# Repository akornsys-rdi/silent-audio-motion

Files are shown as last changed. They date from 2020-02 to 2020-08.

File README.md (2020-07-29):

# Silent audio motion

Silent audio motion, the system behind «Ver no es hablar» artwork

## Description

The device generates the movement of a magnet according to an input audio signal. For this purpose the device generates a PWM signal with polarity (positive and negative half cycle) to excite an electromagnet. This signal is proportional to an analog input signal (audio source). It has two symmetrical channels and it responds to different frequencies, signal levels and waveforms.

This repository includes all the necessary files of this project: The 3D files to be printed, the control board of the device and its firmware.

### Technical features

- Supply voltage: 12VDC
- Frequency range: 1KHz-0.1Hz (firmware capability)
- Input voltage: up to 3Vpp
- Input impedance: 20kΩ

### Status LED

The device includes an LED to show the state it is in, these states are:

- Permanent LED indicates that there is no signal on either channel, the output driver is off.
- Slow blinking LED (~8Hz) indicates clipping on output, input level needs to be lowered or ADJ trimmer needs to be adjusted if not calibrated.
- Fast flashing LED (~30Hz) indicates input level too high, input level needs to be lowered, input stage may be damaged.
- LED off in normal operation.

The status LED may take up to one second to respond to changes in the input.

## Testing the device

### Output driver test

Load the `test_outputs` program. It should generate signals on both output channels. The test firmware can generate different output patterns.
The test is successful when the solenoid connected to each channel moves at the frequency set in code, with the selected waveform.

### Input stage test

Load the 'test_inputs' program. The cursor of the trimmers must not be at the ends. This program must show per port the three inputs of each channel (use serial plotter). Connect an audio source with a signal below 10Hz to both channels.

The test is successful when:

- The values of the first and fourth signals should be the values of the inputs of the left and right audio channels respectively.
- The values of the second and fifth signals should be the values of the ADJ trimmers, and should be different from the ends.
- The values of the third and sixth signals are a comparison of the negative half-cycle with the TRG trimmers, and should show a square signal centered on the peaks of the audio inputs. If this square signal does not appear, move the TRG trimmers until it does.

One of the input signal half-cycles may be slightly smaller than the other.

## Calibrating the device

Set the 3Hz and 3Vpp sine wave signal to channel L, with the program 'test_inputs' loaded.

Adjust the ADJ trimmer immediately above the peak of the input signal, and below the STANDBY_THRESHOLD threshold (default 900). A good value is 817. Turning it counterclockwise increases the value, and turning it clockwise decreases it.

Change the frequency to 0.5Hz. Adjust the ADJ trimmer until it is as close to zero as possible. It should be shown only during negative half-cycles. Values too low show square signals during both half-cycles. Values too high are far from zero on negative half-cycles.
A good adjustment is to lower it until it is below zero and to go up until the trigger disappears in the positive semicircle, then add a quarter turn more. Turning clockwise lowers the value, turning counterclockwise raises it.

Repeat the process with the R channel.

Enter signal on both channels, the setting signals must overlap.

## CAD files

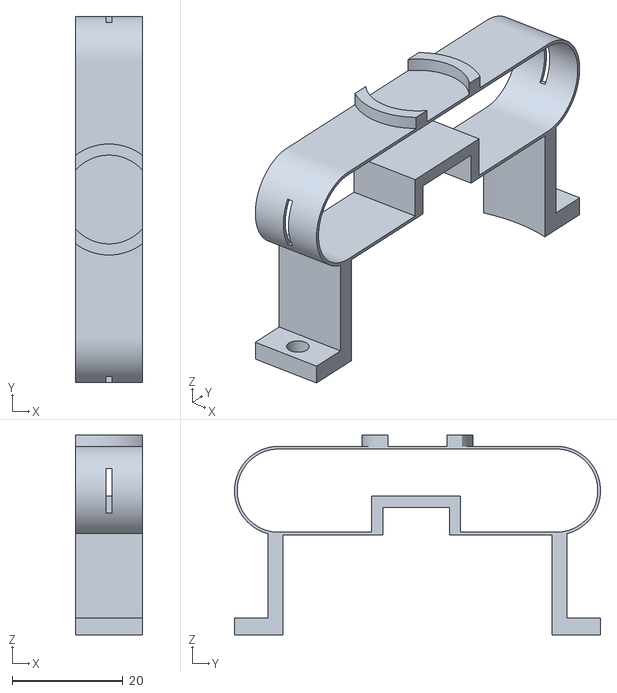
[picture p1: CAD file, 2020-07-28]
3d/bridge.stl
12.0 x 66.0 x 36.0

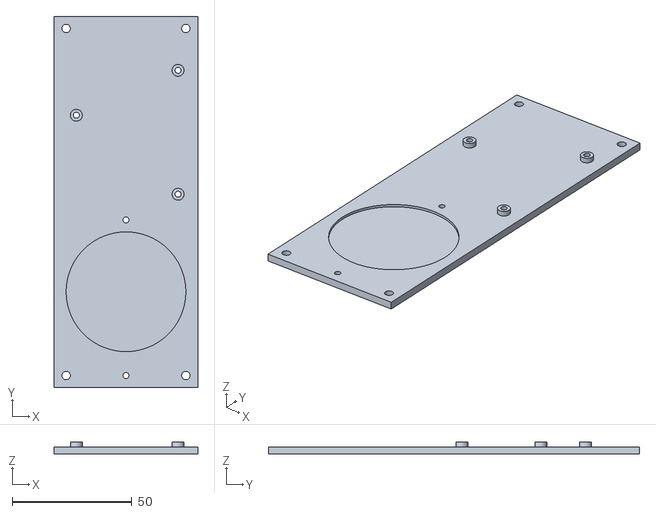
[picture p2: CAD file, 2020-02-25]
3d/base.stl
60.0 x 155.0 x 5.00

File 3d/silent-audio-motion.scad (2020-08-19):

$fn=36;

base();
translate([53,0,1]) cover();
translate([26,37,3]) bridge_v3();
translate([26,37,0]) solenoid();
translate([26,37,3.5+21+12.5]) magnet();
translate([105,72,3]) rotate([0,0,180]) pcb();

module base() {
    radius = 4;
    size_x = 107;
    size_y = 74;
    padding_x = 53;
    padding_y = 4;

    difference() {
        union() {
            union() {
                hull() {
                    for (i = [ [radius,radius + padding_y,0], [radius,size_y - radius - padding_y,0], [padding_x - radius,size_y - radius - padding_y,0], [padding_x - radius,radius + padding_y,0] ]) {
                        translate(i) cylinder(r=radius, h=1);
                    }
                }
                hull() {
                    for (i = [ [padding_x - radius*2,radius + padding_y,0], [padding_x - radius*2,size_y - radius - padding_y,0], [padding_x,radius,0], [padding_x,size_y - radius,0] ]) {
                        translate(i) cylinder(r=radius, h=1);
                    }
                }
                hull() {
                    for (i = [ [padding_x,radius,0], [padding_x,size_y - radius,0], [size_x - radius,size_y - radius,0], [size_x - radius,radius,0] ]) {
                        translate(i) cylinder(r=radius, h=1);
                    }
                }
                hull() {
                    for (i = [ [size_x - radius,radius,0], [size_x + radius,radius,0] ]) {
                        translate(i) cylinder(r=radius, h=1);
                    }
                }
                //refuerzos
                for (i = [ [5,7,1], [5,11,1], [5,67,1], [5,63,1] ]) {
                    hull() {
                        for (j = [0:1:1]) {
                            translate(i) translate([0,0,j]) sphere(r=1, $fn=36);
                            translate(i) translate([45,0,j]) sphere(r=1, $fn=36);
                        }
                    }
                }
            }
            //bridge
            translate([20,padding_y, 0]) cube([12,size_y - padding_y*2, 3]);
            //puntos montaje base
            translate([size_x + radius,radius,0]) cylinder(r=radius, h=3);
            translate([radius,size_y - radius - padding_y,0]) cylinder(r=radius, h=3);
            //punto montaje pcb
            translate([58.25,16.5,0]) cylinder(r=3.5, h=3.25);
            translate([58.25,68.25,0]) cylinder(r=3.5, h=3.25);
            translate([100.75,35.25,0]) cylinder(r=3.5, h=3.25);
        }
        union() {
            //solenoide
            translate([26,37,-1]) cylinder(r=24.5, h=5);
            //vaciado pcb
            hull() {
                for (i = [ [60,25,-1], [60,60,-1], [75,10,-1], [92,60,-1], [92,10,-1] ]) {
                    translate(i) cylinder(r=3, h=3);
                }
            }
            //taladros montaje bridge
            translate([26,7,-1]) cylinder(r=1.25, h=5);
            translate([26,67,-1]) cylinder(r=1.25, h=5);
            //taladros montaje pcb
            translate([58.25,16.5,-1]) cylinder(r=1.25, h=5);
            translate([58.25,68.25,-1]) cylinder(r=1.25, h=5);
            translate([100.75,35.25,-1]) cylinder(r=1.25, h=5);
            //taladros montaje base
            translate([size_x + radius,radius,-1]) cylinder(r=1.75, h=5);
            translate([size_x + radius,radius,0.1]) cylinder(r1=1.75, r2=3, h=3.1);
            translate([radius,size_y - radius - padding_y,-1]) cylinder(r=1.75, h=5);
            translate([radius,size_y - radius - padding_y,0.1]) cylinder(r1=1.75, r2=3, h=3.1);
        }
    }
}

module cover() {
    difference() {
        union() {
            hull() {
                for(i = [ [3,3,0], [3,71,0], [51,3,0], [51,71,0] ]) {
                    translate(i) cylinder(r=3, h=20);
                }
            }
            union() {
                translate([6.75+5.25,0.5,5]) rotate([90,0,0]) linear_extrude(1) text("L", font=":bold", size=4, valign="center", halign = "center");
                translate([6.75,0.5,14]) rotate([90,270,0]) linear_extrude(1) text("TRG", font=":bold", size=4, valign="center", halign = "center");
                translate([6.75+10.5,0.5,14]) rotate([90,270,0]) linear_extrude(1) text("ADJ", font=":bold", size=4, valign="center", halign = "center");
                translate([6.75+5.25+21,0.5,5]) rotate([90,0,0]) linear_extrude(1) text("R", font=":bold", size=4, valign="center", halign = "center");
                translate([6.75+21,0.5,14]) rotate([90,270,0]) linear_extrude(1) text("ADJ", font=":bold", size=4, valign="center", halign = "center");
                translate([6.75+31.5,0.5,14]) rotate([90,270,0]) linear_extrude(1) text("TRG", font=":bold", size=4, valign="center", halign = "center");
                translate([53.5,25,17]) rotate([90,0,90]) linear_extrude(1) text("IN", font=":bold", size=4, valign="center", halign = "center");
                translate([53.5,41.6+2.54,13]) rotate([90,0,90]) linear_extrude(1) text("L", font=":bold", size=4, valign="center", halign = "center");
                translate([53.5,41.6+10.16+2.54,13]) rotate([90,0,90]) linear_extrude(1) text("R", font=":bold", size=4, valign="center", halign = "center");
                translate([53.5,41.6+20.32,13]) rotate([90,0,90]) linear_extrude(1) text("-", font=":bold", size=6, valign="center", halign = "center");
                translate([53.5,41.6+20.32+5.08,13]) rotate([90,0,90]) linear_extrude(1) text("+", font=":bold", size=5, valign="center", halign = "center");
            }
        }
        union() {
            //ventilacion
            translate([10.25,10.25,18]) for(i = [0:7:30]) {
                for(j = [0:7:50]) {
                    translate([i,j,0]) cube([4.5,4.5,3]);
                }
            }
            //puntos de montaje
            difference() {
                hull() {
                    for(i = [ [4,4,-1], [4,70,-1], [50,4,-1], [50,70,-1] ]) {
                        translate(i) cylinder(r=3, h=20);
                    }
                }
                translate([5.25,16.5,3.75]) cylinder(r=3.75, h=17);
                translate([5.25,68.25,3.75]) cylinder(r=3.75, h=17);
                translate([47.75,35.25,3.75]) cylinder(r=3.75, h=17);
            }
            //pot
            translate([6.75,2,7.1]) for(i = [0:10.5:35]) {
                translate([i,0,0]) rotate([90,0,0]) cylinder(r=1.5, h=3);
            }
            //jack
            translate([52,25,10]) hull() {
                rotate([0,90,0]) cylinder(r=4, h=3);
                translate([0,0,-10]) rotate([0,90,0])  cylinder(r=4, h=3);
            }
            //conn
            translate([52,39.6,0]) for(i = [0:5.08:26]) {
                translate([0,i,6]) cube([3,4,4.5]);
                translate([-4,i+2,18]) cylinder(r=2.5, h=3);
            }
            //puntos de montaje
            union() {
                translate([5.25,16.5,3]) cylinder(r=1.75, h=3);
                translate([5.25,68.25,3]) cylinder(r=1.75, h=3);
                translate([47.75,35.25,3]) cylinder(r=1.75, h=3);
                translate([5.25,16.5,4.75]) cylinder(r=2.85, h=16);
                translate([5.25,68.25,4.75]) cylinder(r=2.85, h=16);
                translate([47.75,35.25,4.75]) cylinder(r=2.85, h=16);
            }
        }
    }
}

module bridge_v3() {
    thickness = 0.5;
    aperture = 1;
    lenght = 50;

    difference() {
        union() {
            //base
            translate([-6,-33,0]) cube([12,66,3]);
            translate([-6,-27,0]) cube([12,54,32.5]);
            //anillo
            translate([-6,-(lenght/2),26]) hull() {
                rotate([0,90,0]) cylinder(r=8, h=12);
                translate([0,lenght,0]) rotate([0,90,0]) cylinder(r=8, h=12);
            }
            //soporte iman
            translate([0,0,34]) cylinder(r=10, h=2);
        }
        union() {
            //solenoide
            translate([0,0,-1]) cylinder(r=25, h=19);
            //apertura
            translate([(12-aperture)/2-6,-(lenght/2)-10,22]) cube([aperture,10,8]);
            translate([(12-aperture)/2-6,(lenght/2),22]) cube([aperture,10,8]);
            //hueco anillo
            difference() {
                translate([-7,-(lenght/2),26]) hull() {
                    rotate([0,90,0]) cylinder(r=8-thickness, h=14);
                    translate([0,lenght,0]) rotate([0,90,0]) cylinder(r=8-thickness, h=14);
                }
                //tope
                translate([-8,-8.25,18]) cube([16, 16, 7]);
            }
            //hueco tope
            translate([-9,-6.25,16]) cube([18,12,7]);
            //cortes soporte iman
            translate([0,0,34]) cylinder(r=8, h=3);
            translate([-11,-10,32.5]) cube([5,20,4]);
            translate([6,-10,32.5]) cube([5,20,4]);
            //taladros montaje
            translate([0,-30,-1]) cylinder(r=1.75, h=5);
            translate([0,30,-1]) cylinder(r=1.75, h=5);
        }
    }
}
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

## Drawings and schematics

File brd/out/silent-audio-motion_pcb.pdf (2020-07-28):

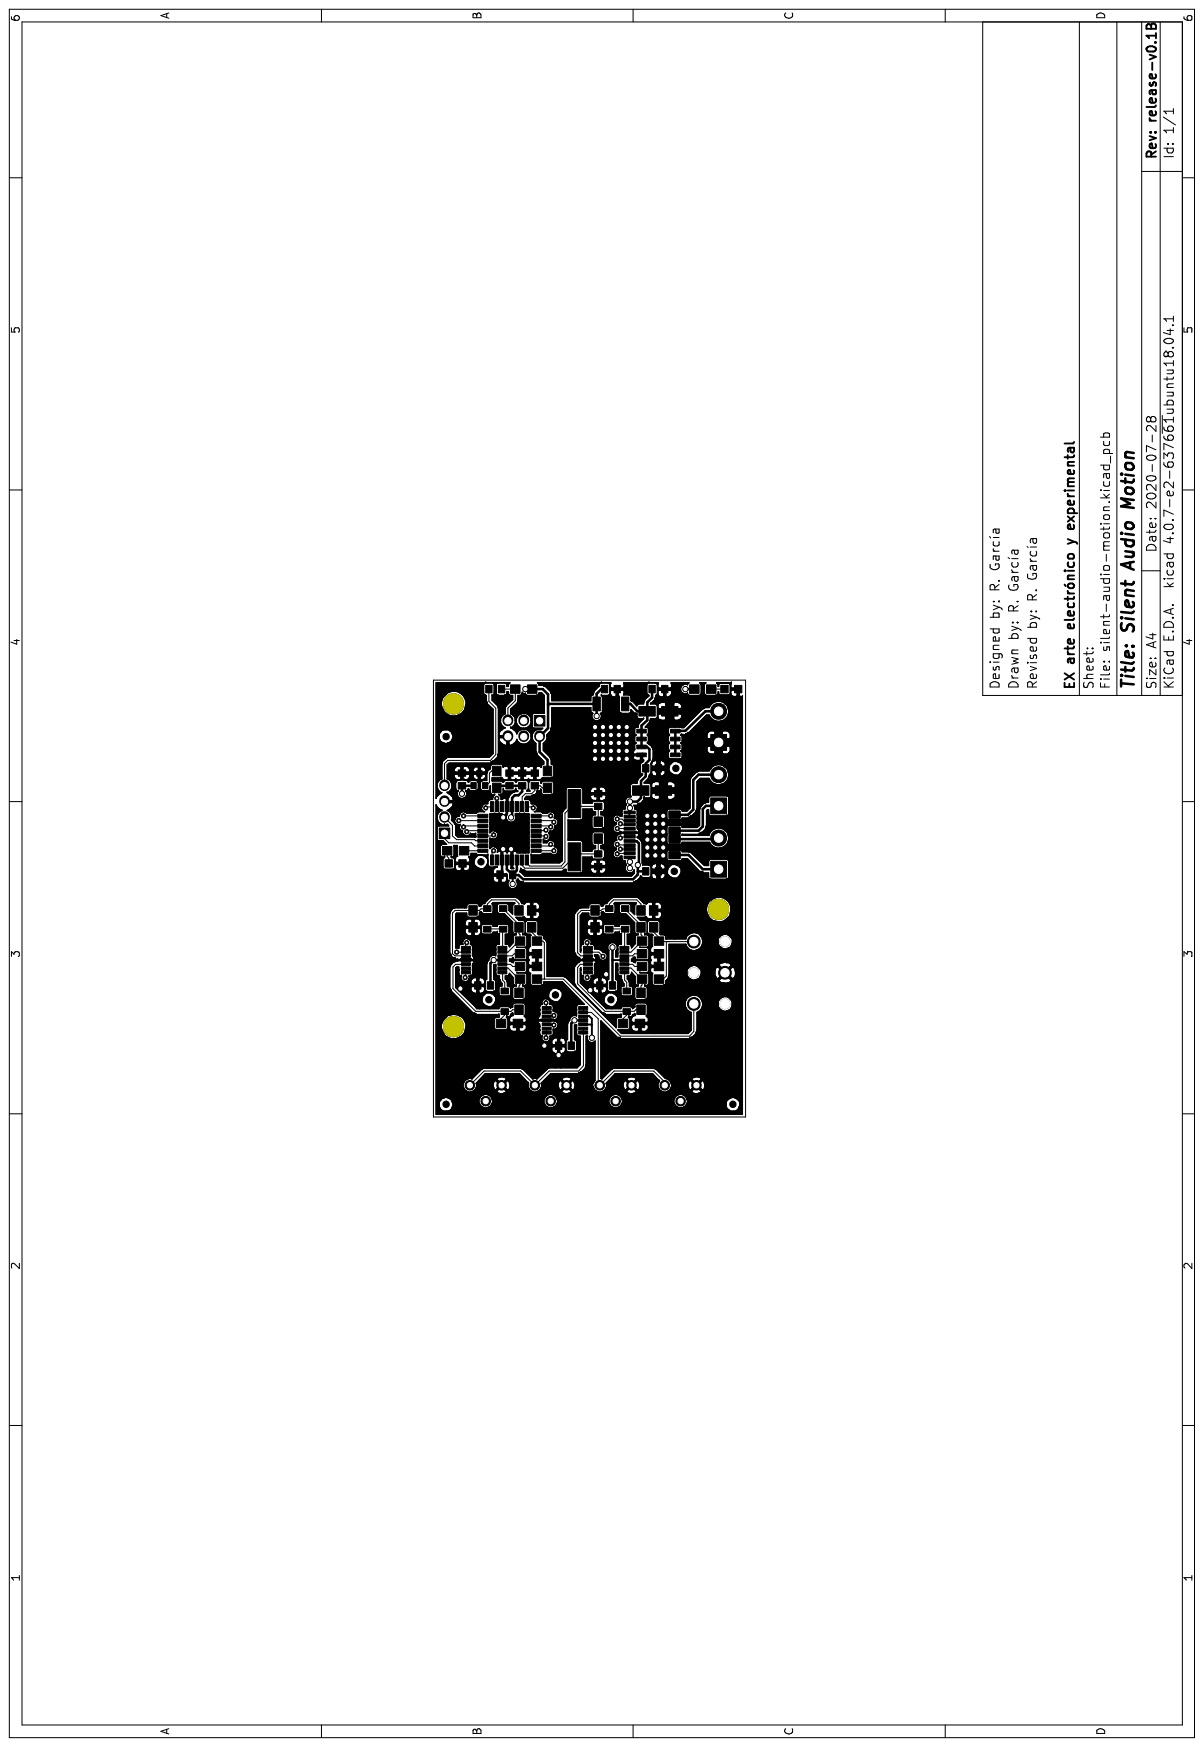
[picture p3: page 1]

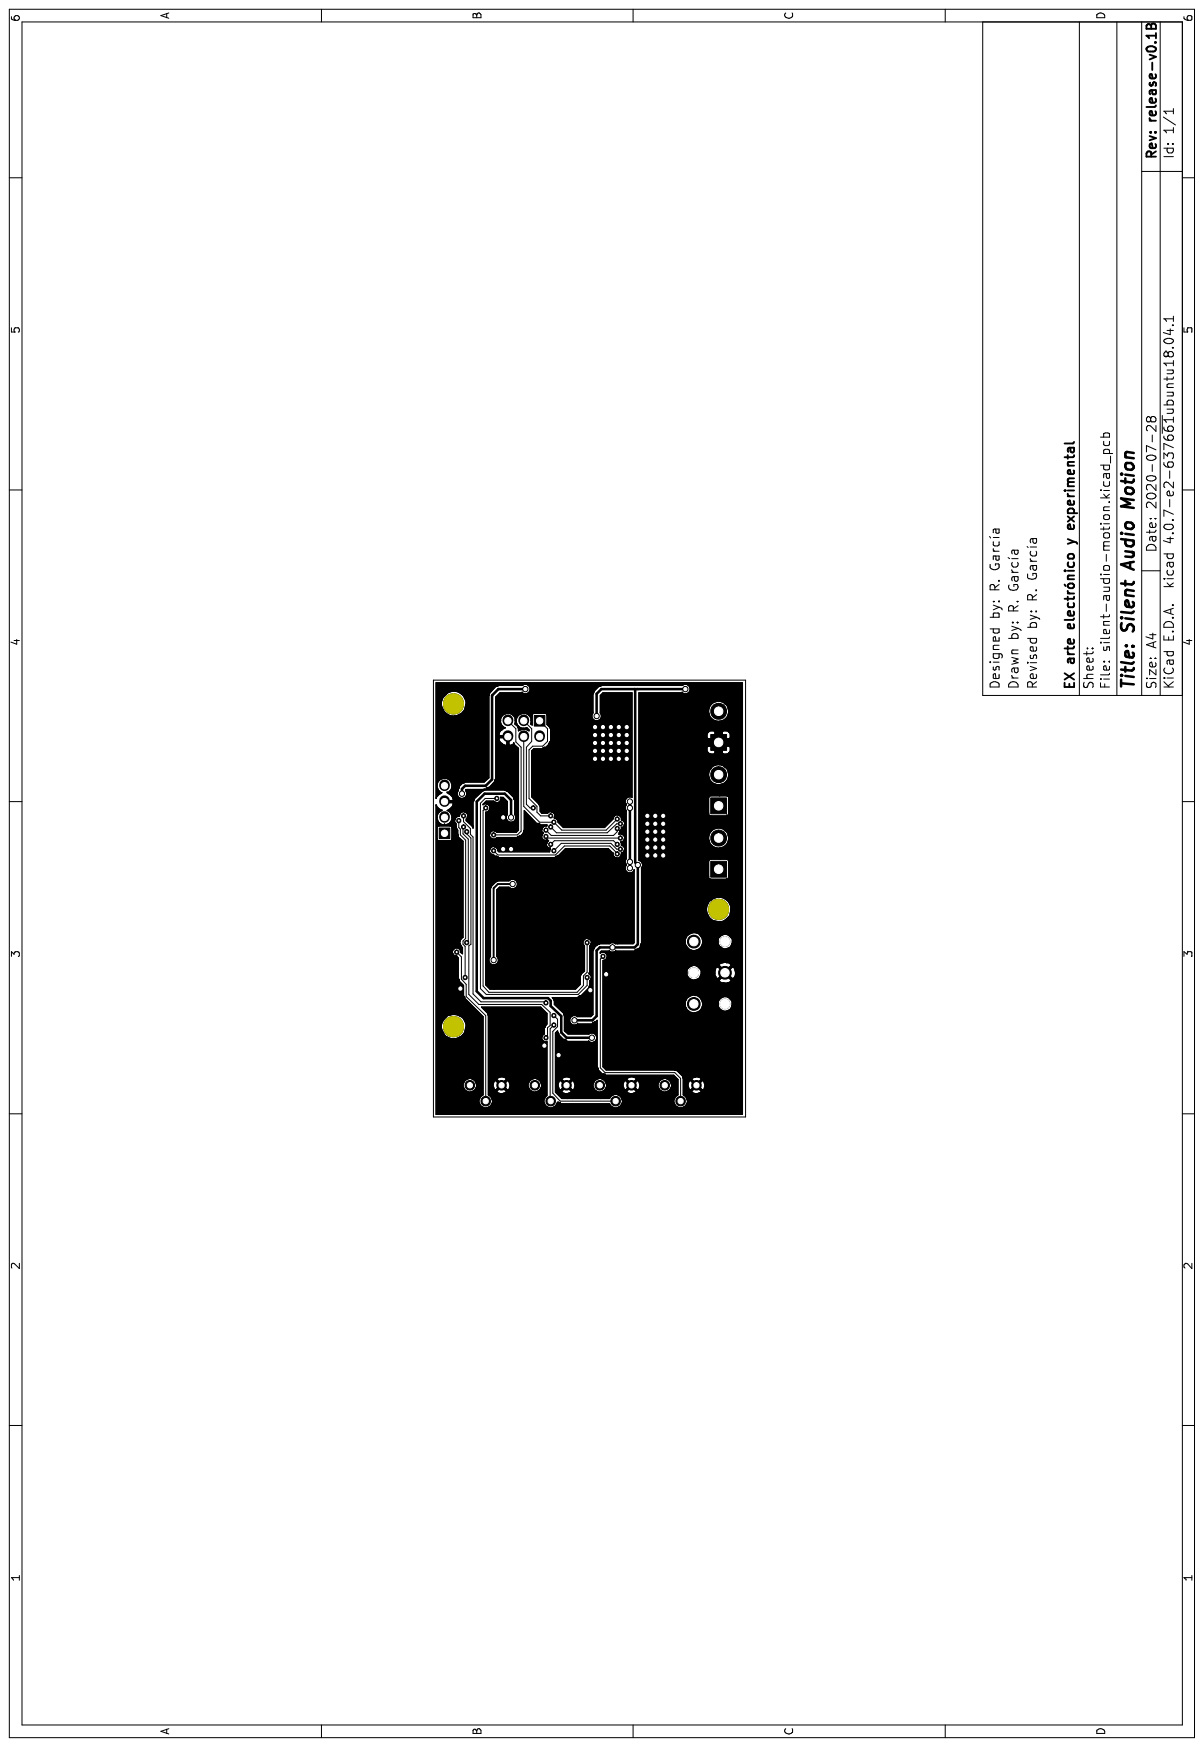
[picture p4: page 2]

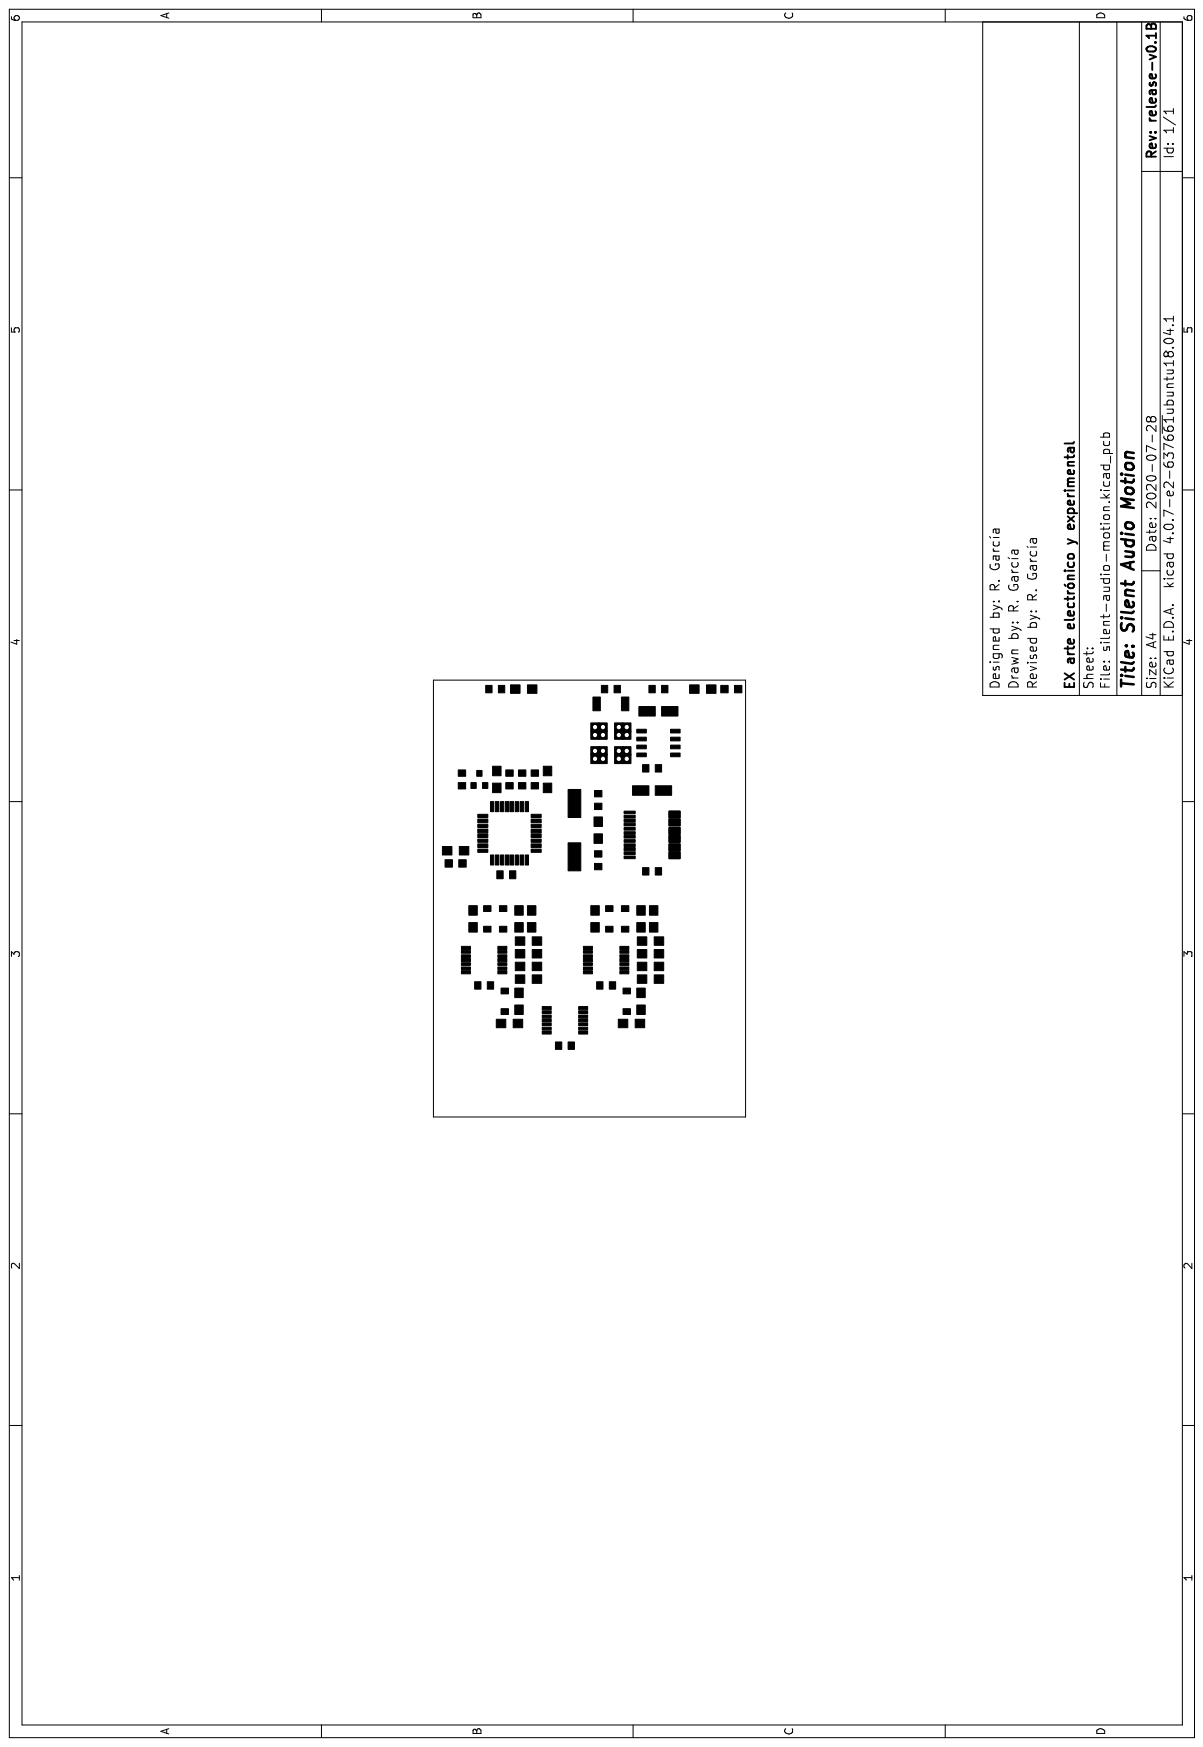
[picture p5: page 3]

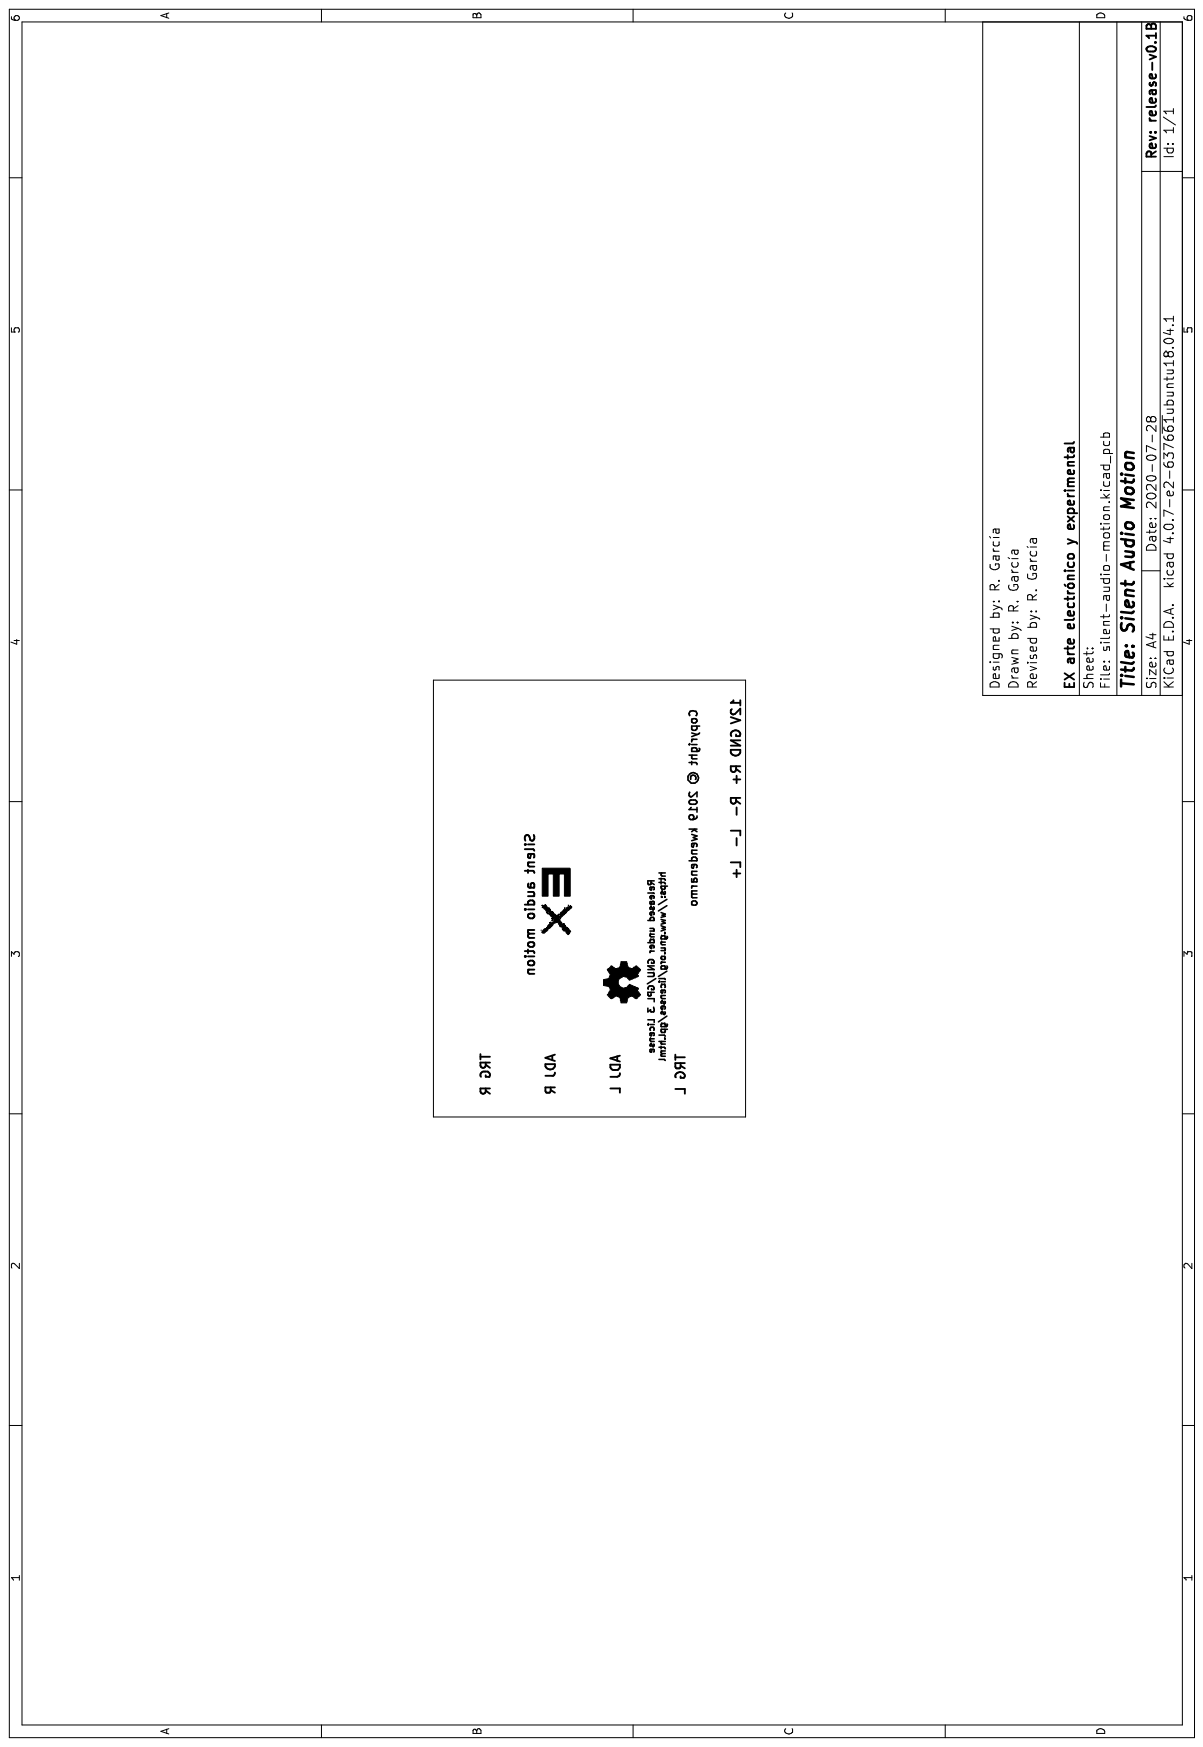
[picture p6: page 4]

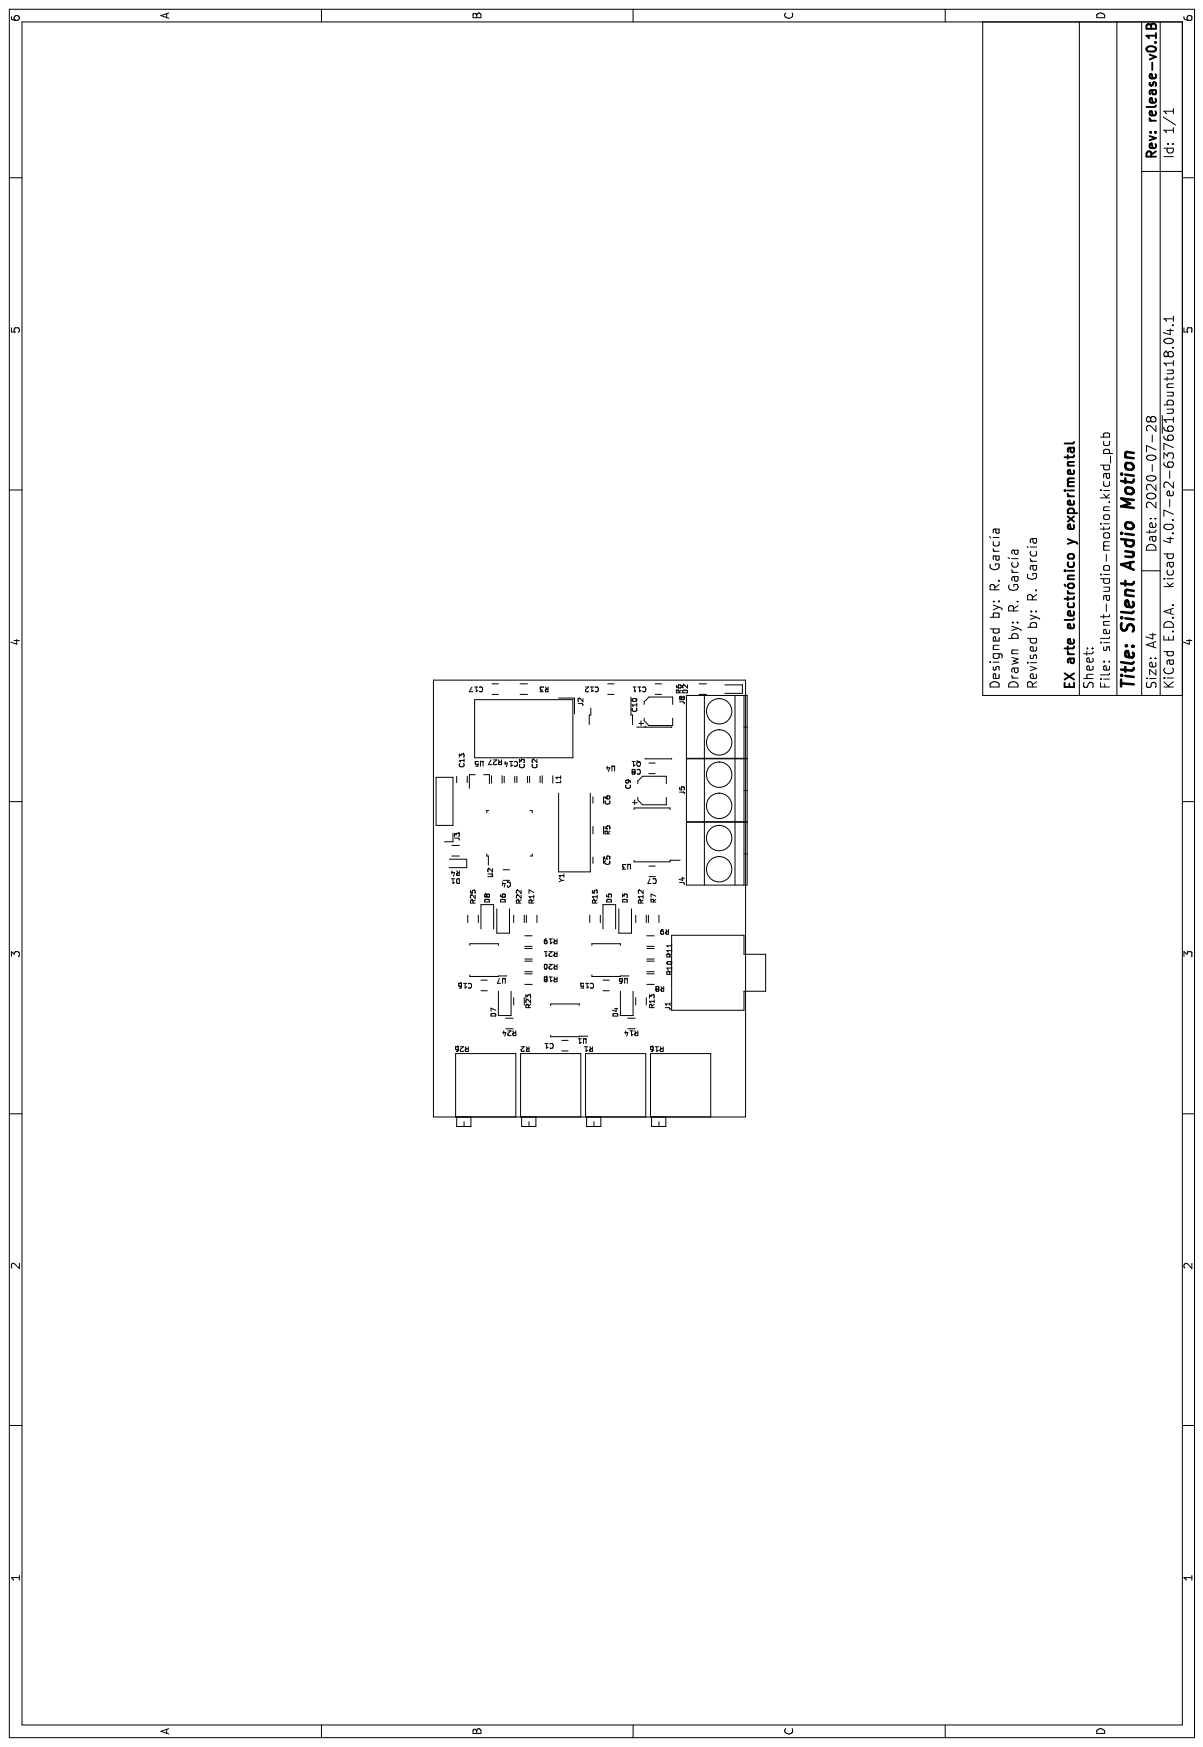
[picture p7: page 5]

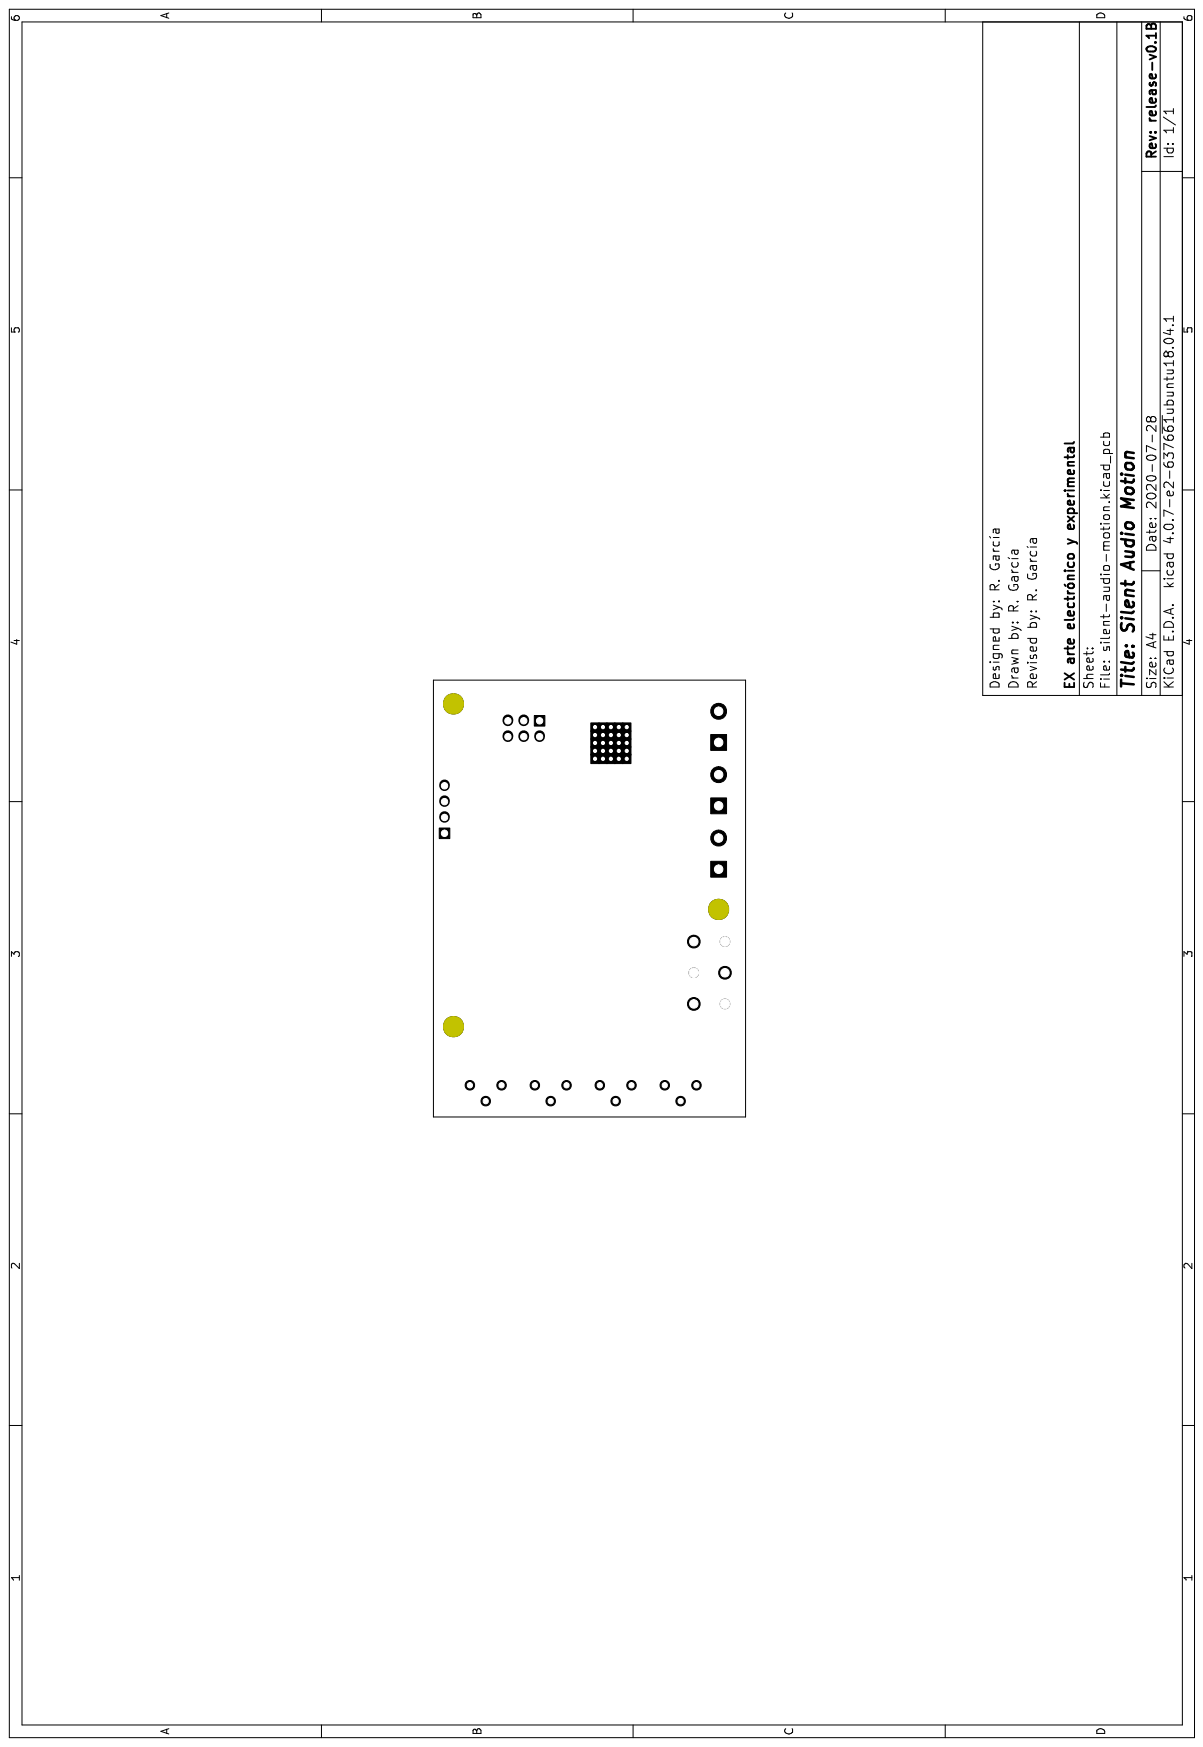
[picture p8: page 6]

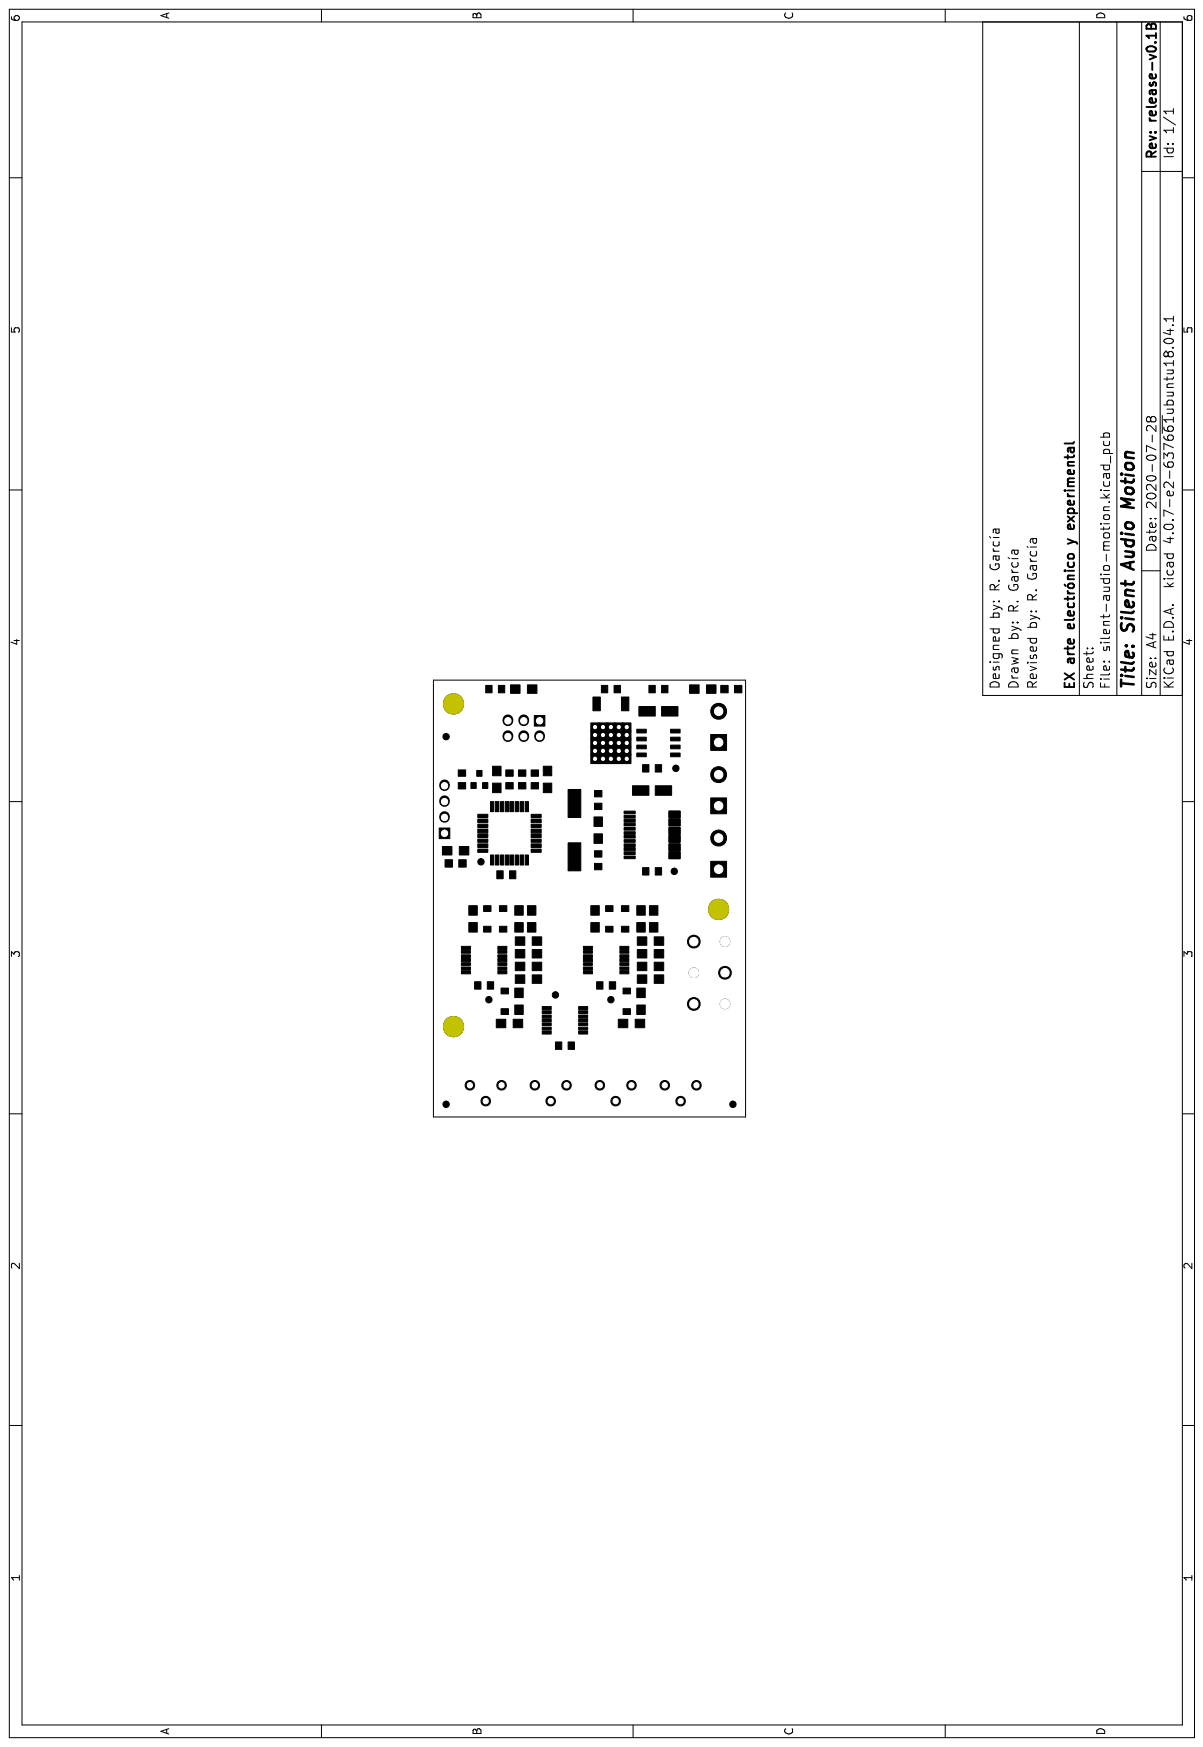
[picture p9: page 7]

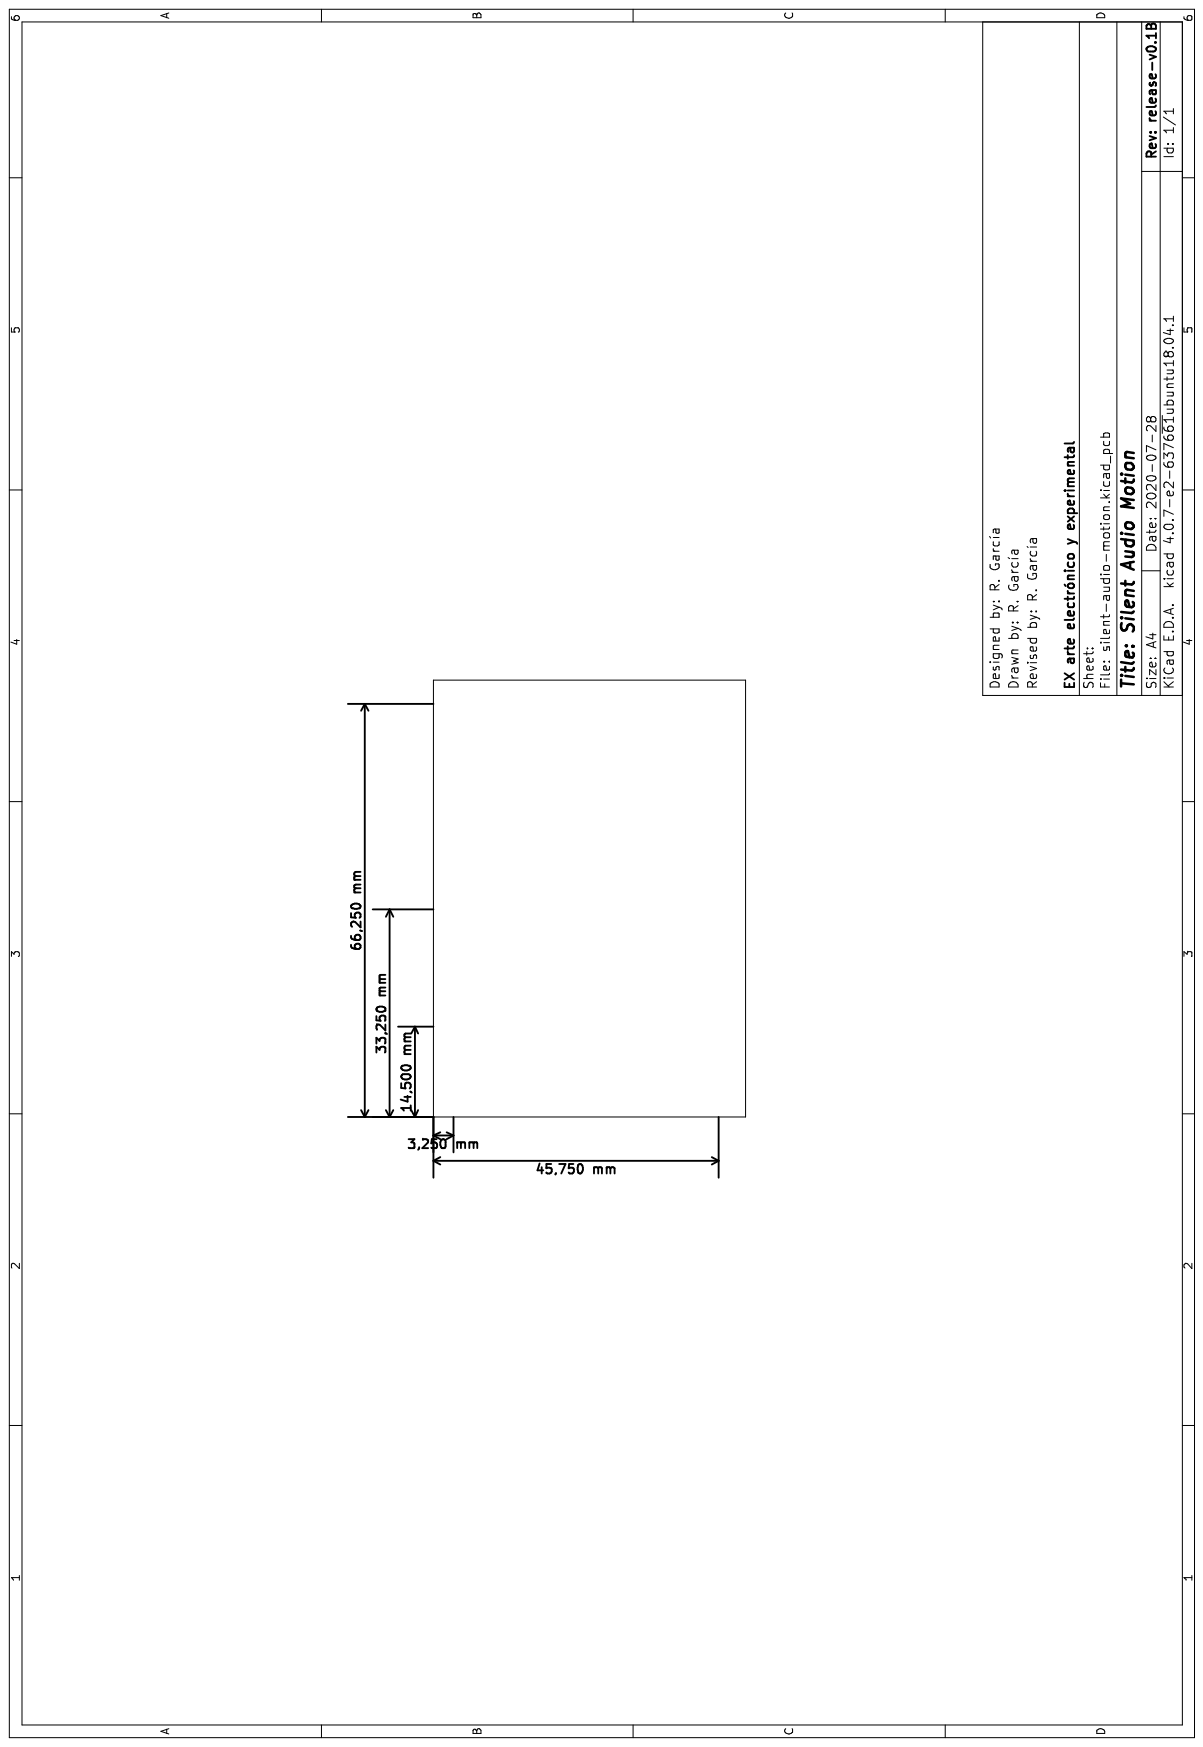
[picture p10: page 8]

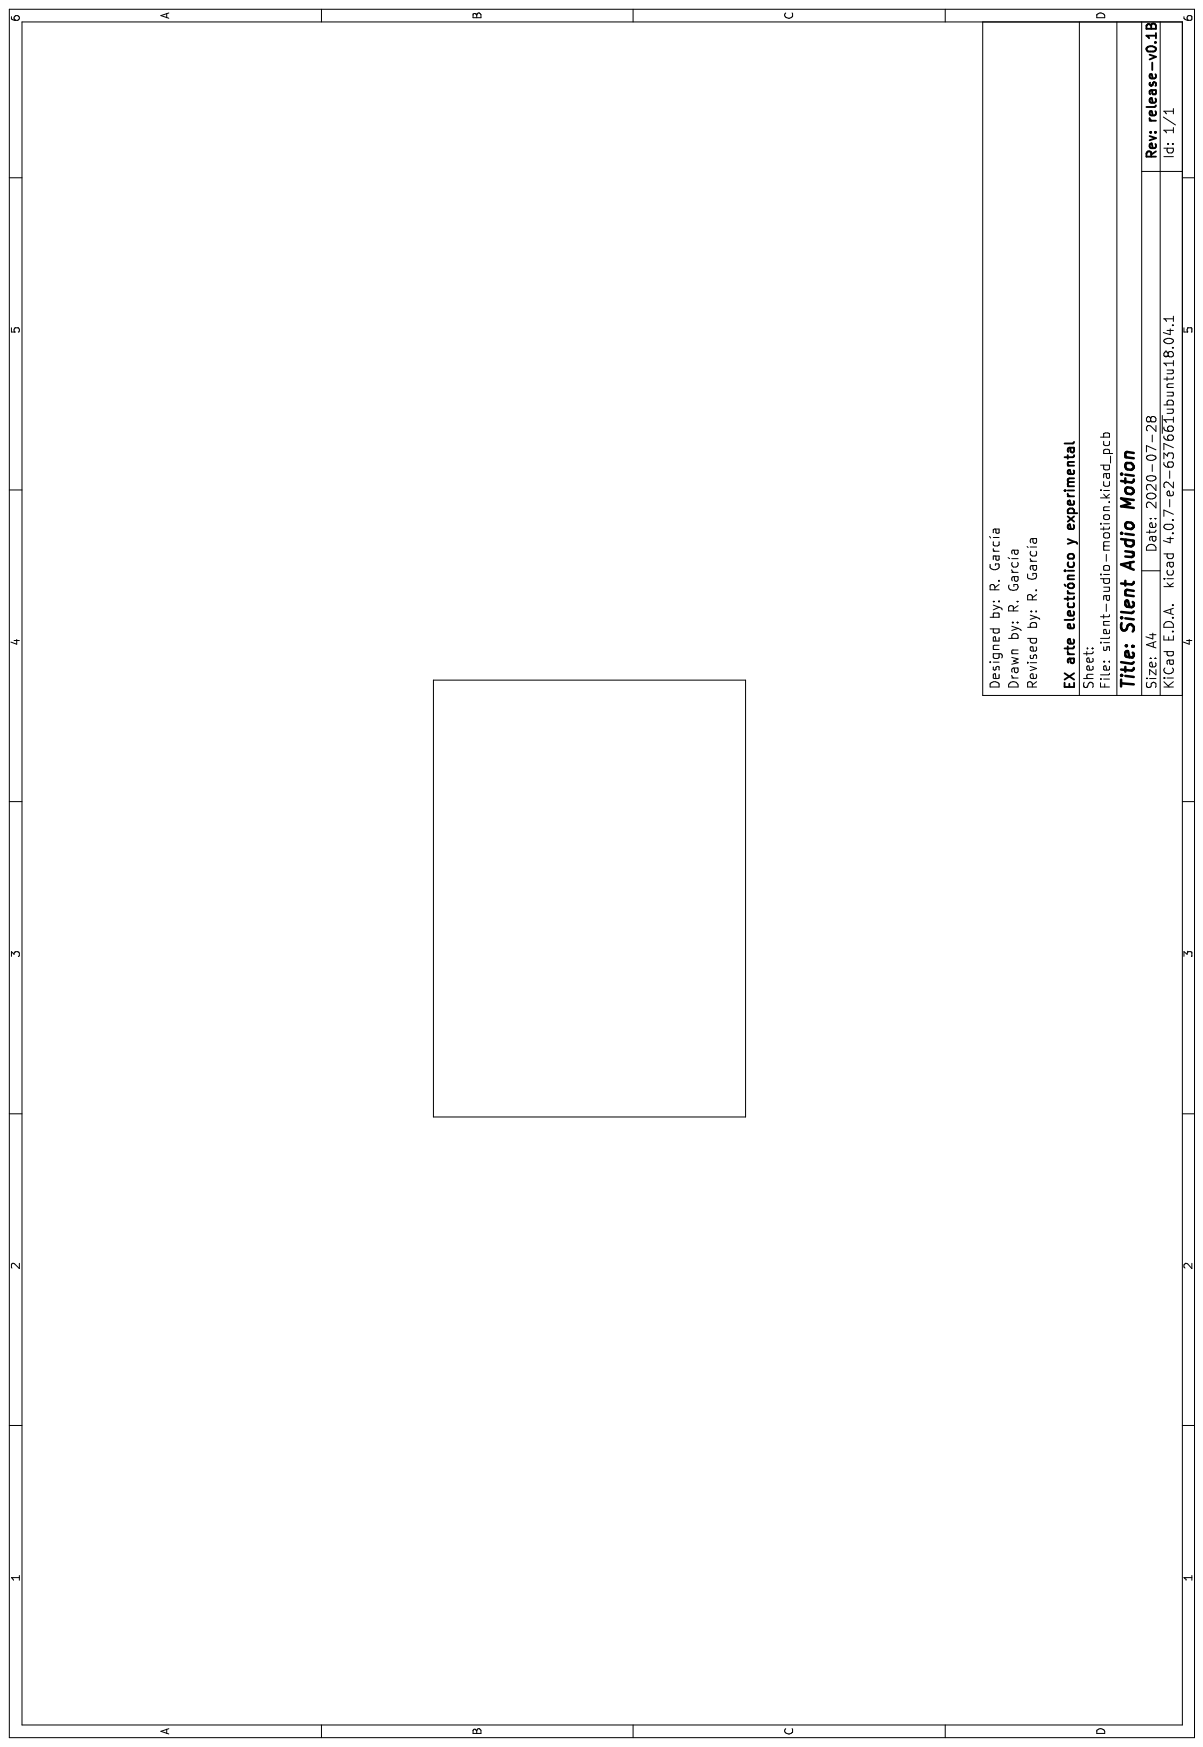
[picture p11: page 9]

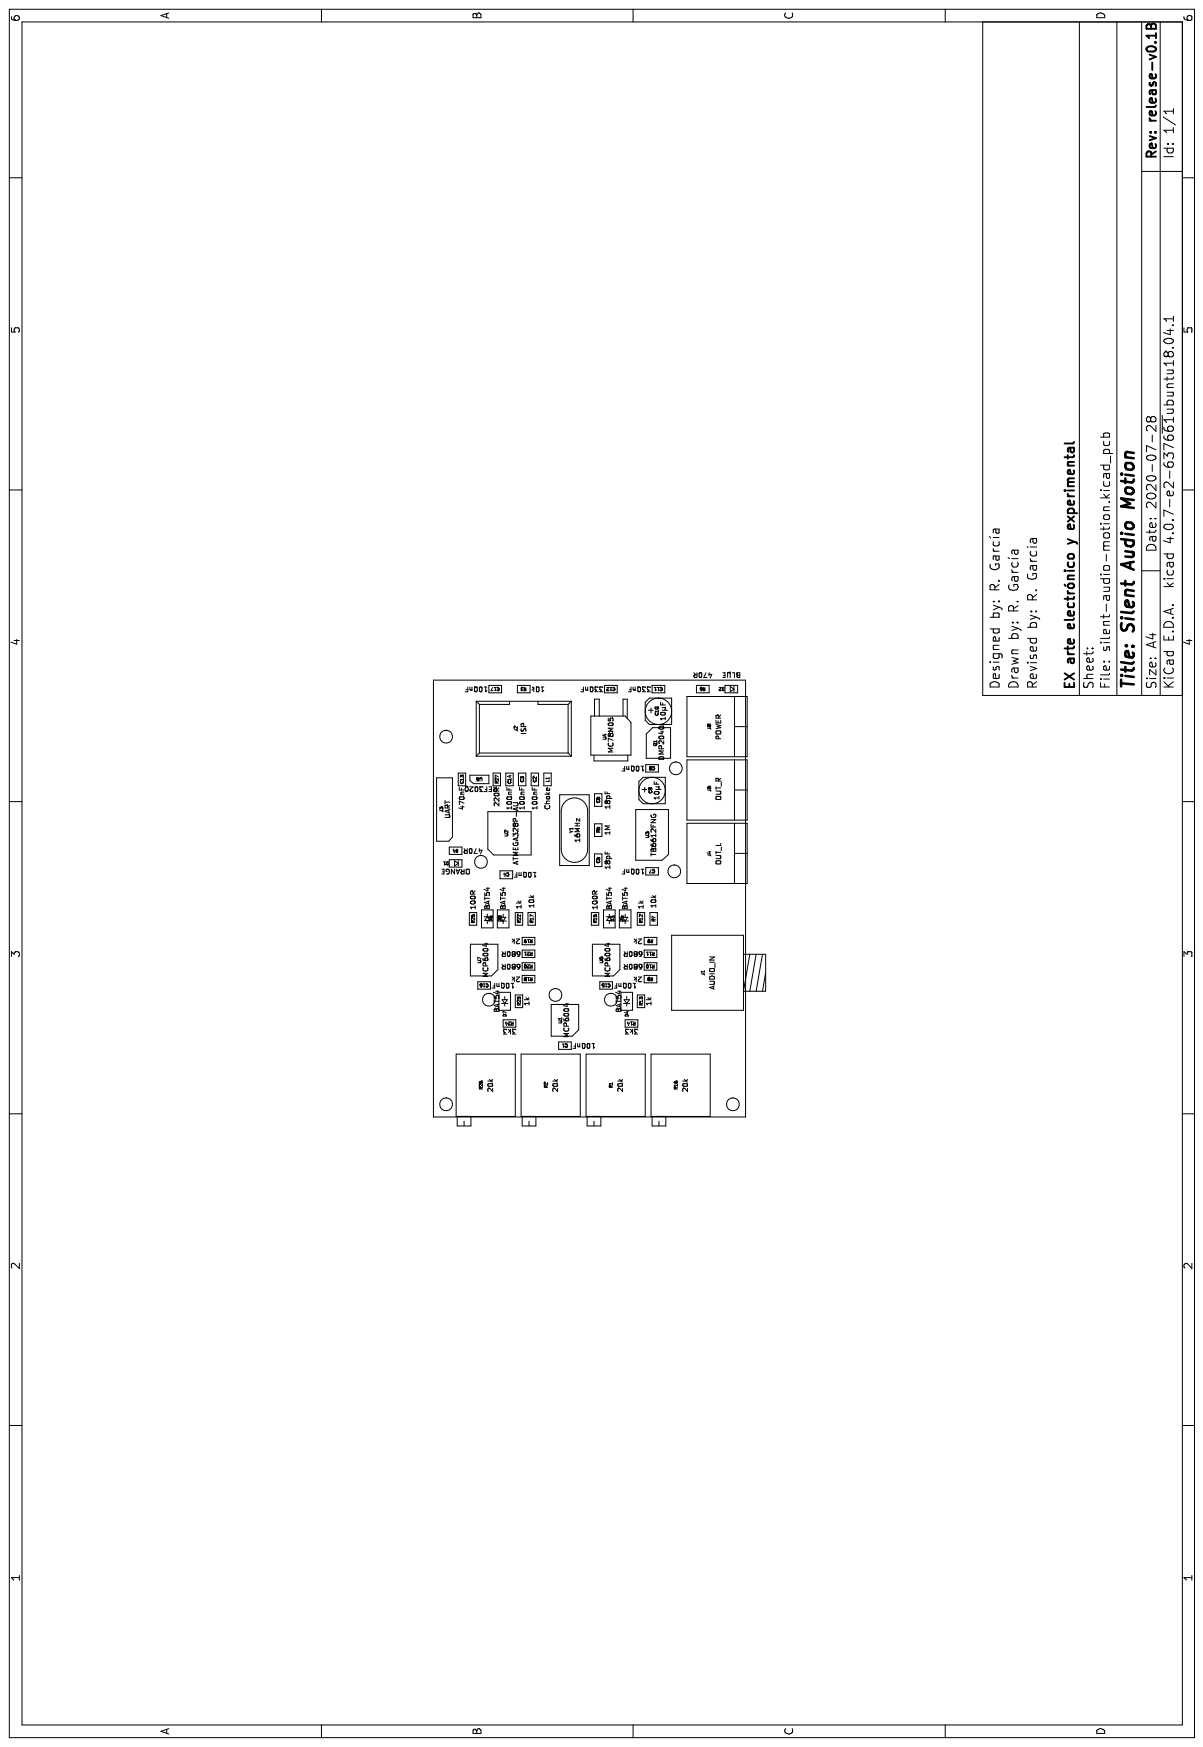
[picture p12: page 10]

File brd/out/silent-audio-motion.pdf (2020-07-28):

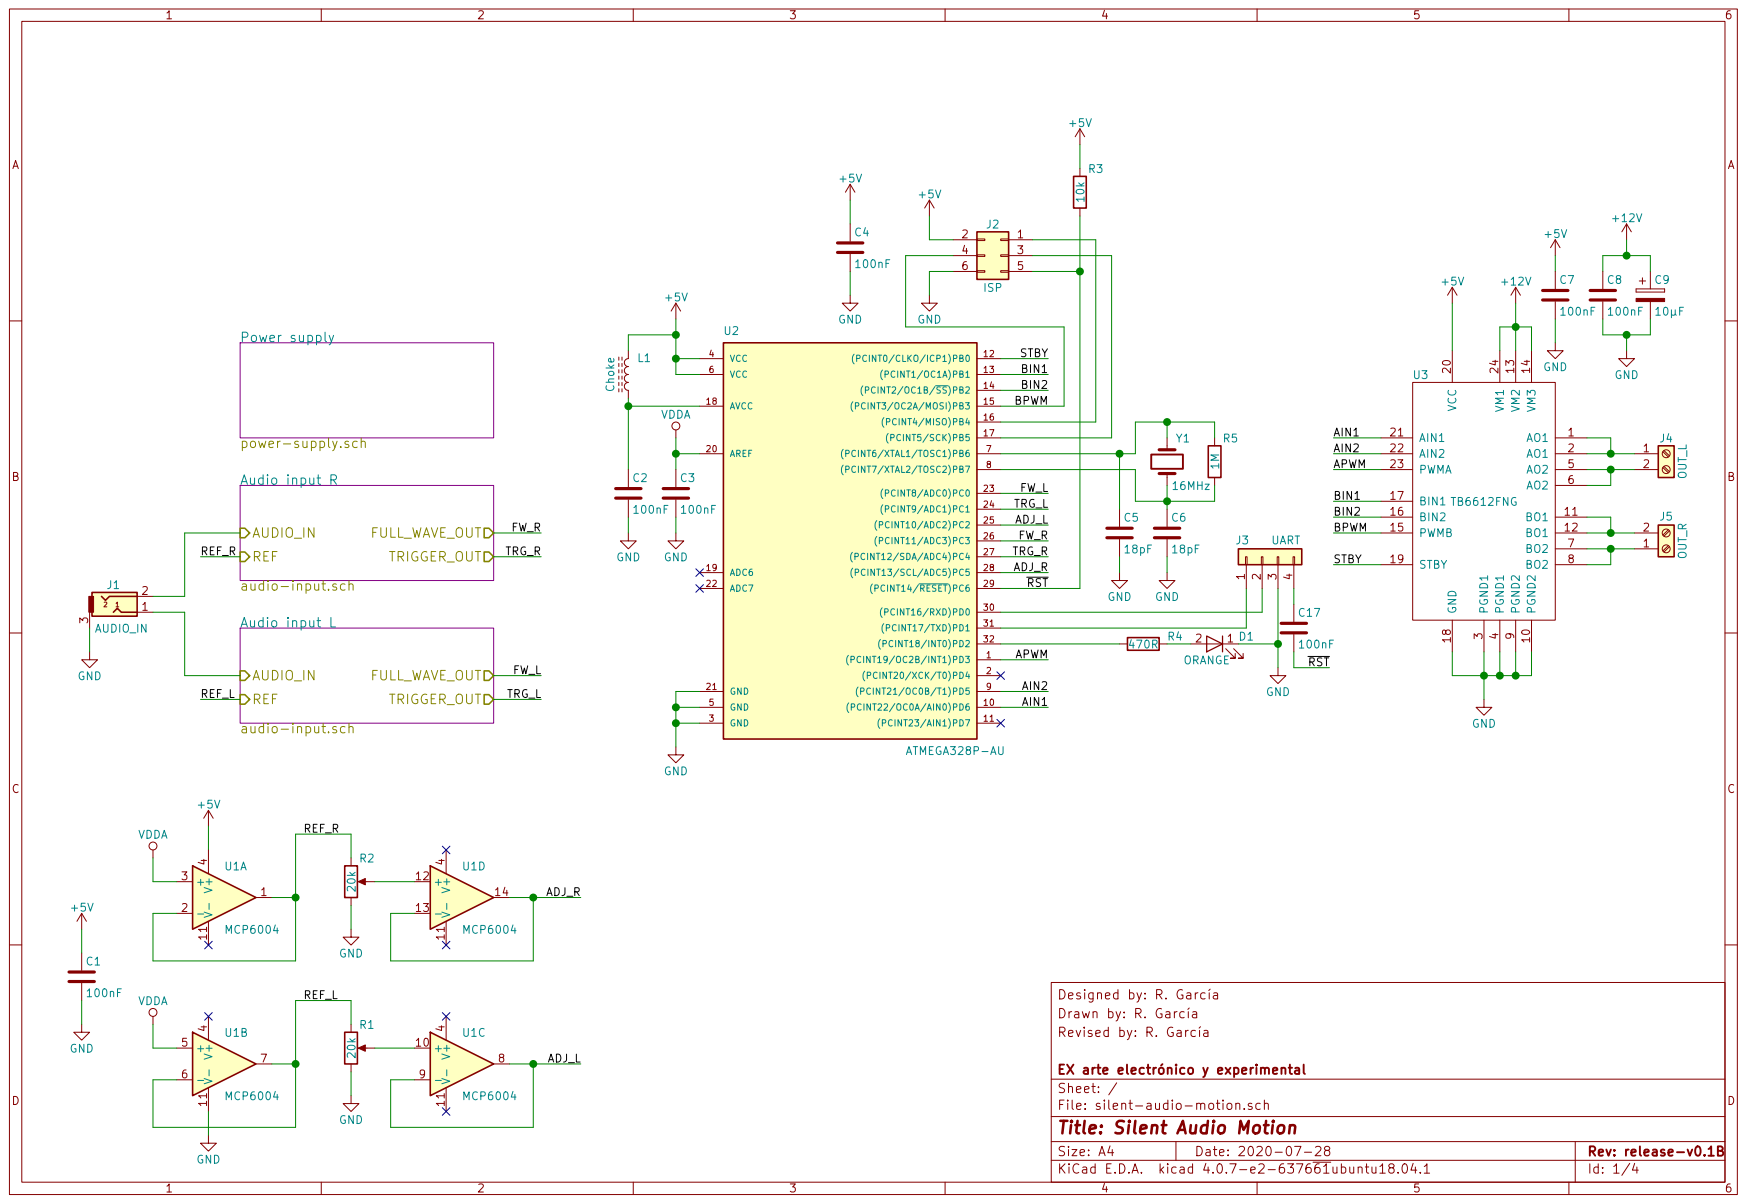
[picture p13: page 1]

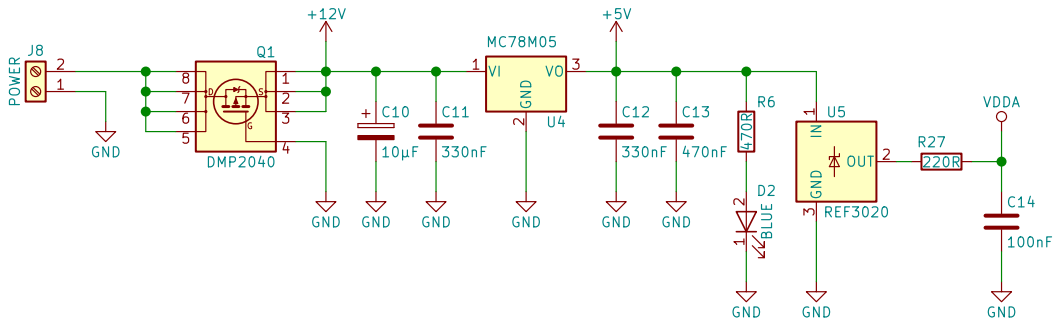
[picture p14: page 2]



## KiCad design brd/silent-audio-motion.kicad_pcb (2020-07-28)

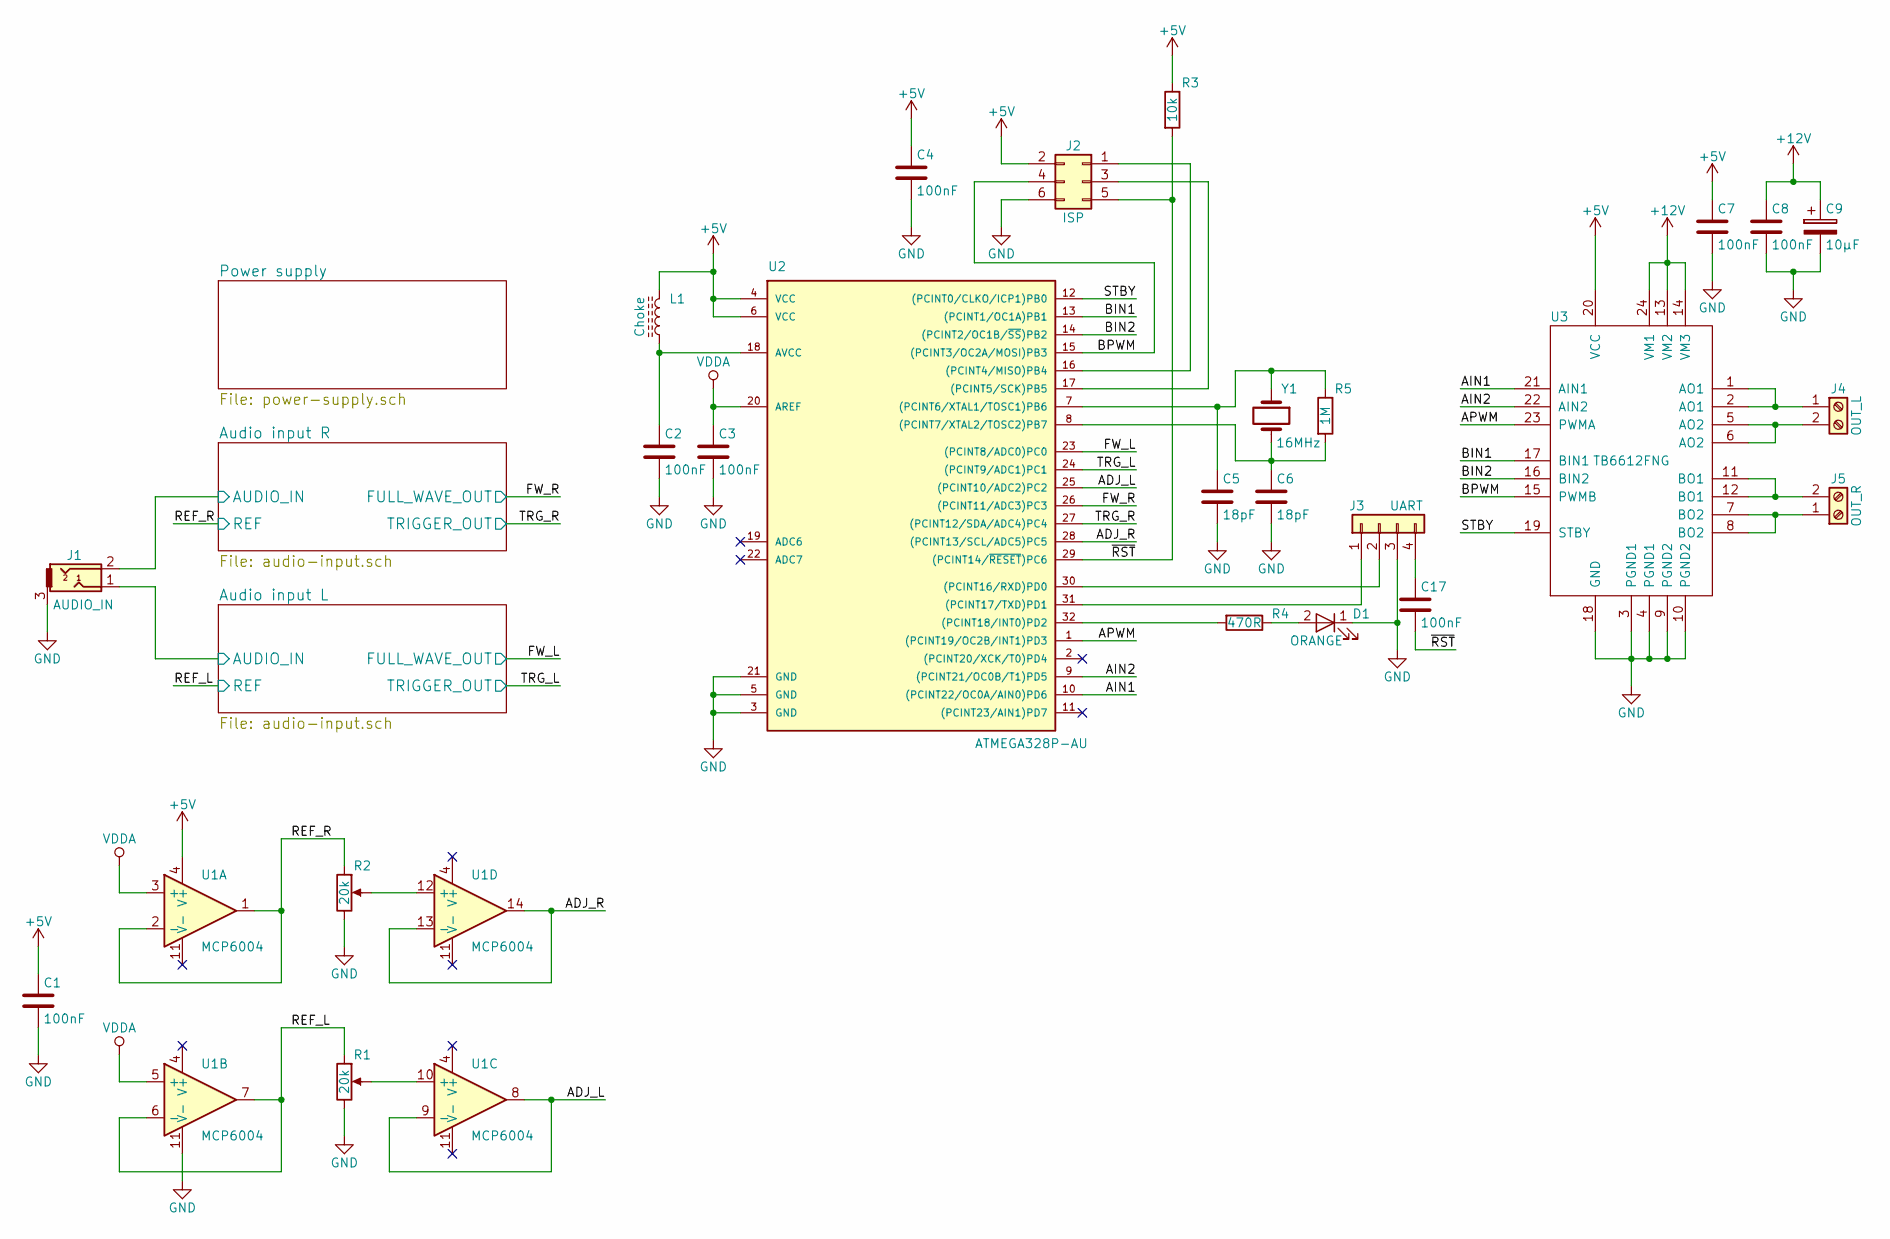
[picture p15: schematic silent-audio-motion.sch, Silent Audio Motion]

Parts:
C1, C2, C3, C4, C7, C8, C17: 100nF; C_0805; Manufacturer Part Number C0805C104J5RACTU
C5, C6: 18pF; C_0805; Manufacturer Part Number C0805C180J5GAC
C9: 10µF; CP_Elec_4x5.3; Manufacturer Part Number UWJ1C100MCL1GB
D1: ORANGE; LED_0805; Manufacturer Part Number LO R976-PS-1
J1: AUDIO_IN; STX-3200-3; Manufacturer Part Number STX-3200-3NB
J2: ISP; IDC-Header_2x03_Pitch2.54mm_Straight
J3: UART; Pin_Header_Straight_1x04_Pitch2.54mm
J4: OUT_L; TerminalBlock_Phoenix_MKDS1.5-2pol; Manufacturer Part Number 1888687
J5: OUT_R; TerminalBlock_Phoenix_MKDS1.5-2pol; Manufacturer Part Number 1888687
L1: Choke; L_0805_HandSoldering; Manufacturer Part Number BLM21PG331SN1D
R1, R2: 20k; Potentiometer_Trimmer_Bourns_3299P; Manufacturer Part Number 36KR20KLF
R3: 10k; R_0805_HandSoldering; Manufacturer Part Number CR0805-JW-103ELF
R4: 470R; R_0805_HandSoldering; Manufacturer Part Number CR0805-JW-471ELF
R5: 1M; R_0805_HandSoldering; Manufacturer Part Number CR0805-JW-105ELF
U1: MCP6004; TSSOP-14_4.4x5mm_Pitch0.65mm; Manufacturer Part Number MCP6004-I/ST
U2: ATMEGA328P-AU; TQFP-32_7x7mm_Pitch0.8mm; Manufacturer Part Number ATMEGA328P-AU
U3: TB6612FNG; SSOP-24_5.3x8.2mm_Pitch0.65mm; Manufacturer Part Number TB6612FNG,C,8,EL
Y1: 16MHz; Crystal_SMD_HC49-SD; Manufacturer Part Number ABLS-16.000MHZ-B4-T

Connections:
+5V: C1.1, C4.1, C7.1, J2.2, L1.2, R3.1, U1.4 (V+), U2.4 (VCC), U2.6 (VCC), U3.20 (VCC); also elsewhere on the board
+12V: C8.1, C9.1, U3.13 (VM2), U3.14 (VM3), U3.24 (VM1); also elsewhere on the board
/ADJ_L: U1.8, U1.9 (-), U2.25 ((PCINT10/ADC2)PC2)
/ADJ_R: U1.13 (-), U1.14, U2.28 ((PCINT13/SCL/ADC5)PC5)
/AIN1: U2.10 ((PCINT22/OC0A/AIN0)PD6), U3.21 (AIN1)
/AIN2: U2.9 ((PCINT21/OC0B/T1)PD5), U3.22 (AIN2)
/APWM: U2.1 ((PCINT19/OC2B/INT1)PD3), U3.23 (PWMA)
/Audio input L/AUDIO_IN: J1.1; also elsewhere on the board
/Audio input R/AUDIO_IN: J1.2; also elsewhere on the board
/BIN1: U2.13 ((PCINT1/OC1A)PB1), U3.17 (BIN1)
/BIN2: U2.14 ((PCINT2/OC1B/~SS~)PB2), U3.16 (BIN2)
/BPWM: J2.4, U2.15 ((PCINT3/OC2A/MOSI)PB3), U3.15 (PWMB)
/FW_L: U2.23 ((PCINT8/ADC0)PC0); also elsewhere on the board
/FW_R: U2.26 ((PCINT11/ADC3)PC3); also elsewhere on the board
/REF_L: R1.1, U1.6 (-), U1.7; also elsewhere on the board
/REF_R: R2.1, U1.1, U1.2 (-); also elsewhere on the board
/STBY: U2.12 ((PCINT0/CLKO/ICP1)PB0), U3.19 (STBY)
/TRG_L: U2.24 ((PCINT9/ADC1)PC1); also elsewhere on the board
/TRG_R: U2.27 ((PCINT12/SDA/ADC4)PC4); also elsewhere on the board
/~RST: C17.2, J2.5, R3.2, U2.29 ((PCINT14/~RESET~)PC6)
GND: C1.2, C2.2, C3.2, C4.2, C5.2, C6.2, C7.2, C8.2, C9.2, D1.1 (K), J1.3, J2.6, J3.3, R1.3, R2.3, U1.11 (V-), U2.3 (GND), U2.5 (GND), U2.21 (GND), U3.3 (PGND1), U3.4 (PGND1), U3.9 (PGND2), U3.10 (PGND2), U3.18 (GND); also elsewhere on the board
unnamed: C2.1, L1.1, U2.18 (AVCC)
unnamed: C5.1, R5.1, U2.7 ((PCINT6/XTAL1/TOSC1)PB6), Y1.1
unnamed: C6.1, R5.2, U2.8 ((PCINT7/XTAL2/TOSC2)PB7), Y1.2
unnamed: C17.1, J3.4
unnamed: D1.2 (A), R4.1
unnamed: J2.1, U2.16 ((PCINT4/MISO)PB4)
unnamed: J2.3, U2.17 ((PCINT5/SCK)PB5)
unnamed: J3.1, U2.31 ((PCINT17/TXD)PD1)
unnamed: J3.2, U2.30 ((PCINT16/RXD)PD0)
unnamed: J4.1, U3.1 (AO1), U3.2 (AO1)
unnamed: J4.2, U3.5 (AO2), U3.6 (AO2)
unnamed: J5.1, U3.7 (BO2), U3.8 (BO2)
unnamed: J5.2, U3.11 (BO1), U3.12 (BO1)
unnamed: R1.2, U1.10 (+)
unnamed: R2.2, U1.12 (+)
unnamed: R4.2, U2.32 ((PCINT18/INT0)PD2)
VDDA: C3.1, U1.3 (+), U1.5 (+), U2.20 (AREF); also elsewhere on the board

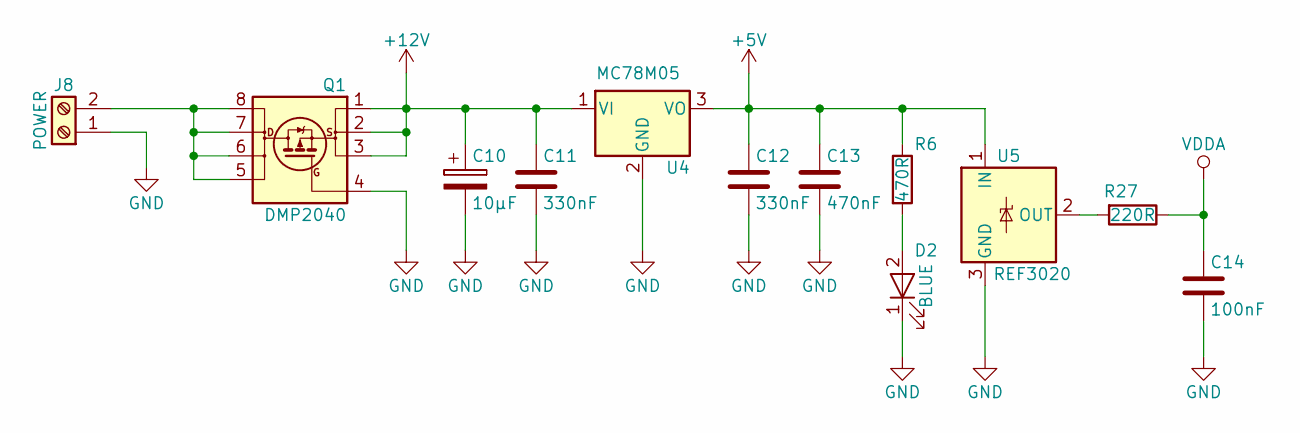
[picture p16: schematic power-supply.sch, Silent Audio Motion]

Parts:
C10: 10µF; CP_Elec_4x5.3; Manufacturer Part Number UWJ1C100MCL1GB
C11, C12: 330nF; C_0805; Manufacturer Part Number GMK212B7334KG-T
C13: 470nF; C_0805; Manufacturer Part Number TMK212BJ474KD-T
C14: 100nF; C_0805; Manufacturer Part Number C0805C104J5RACTU
D2: BLUE; LED_0805; Manufacturer Part Number APHCM2012QBC/D-F01
J8: POWER; TerminalBlock_Phoenix_MKDS1.5-2pol; Manufacturer Part Number 1888687
Q1: DMP2040; SOIC-8_3.9x4.9mm_Pitch1.27mm; Manufacturer Part Number DMP2040USS-13
R6: 470R; R_0805_HandSoldering; Manufacturer Part Number CR0805-JW-471ELF
R27: 220R; R_0805_HandSoldering; Manufacturer Part Number CR0805-JW-221ELF
U4: MC78M05; TO-252-2; Manufacturer Part Number MC78M05CDTRKG
U5: REF3020; SOT-23; Manufacturer Part Number REF3020AIDBZR

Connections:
+5V: C12.1, C13.1, R6.1, U4.3 (VO), U5.1 (IN); also elsewhere on the board
+12V: C10.1, C11.1, Q1.1 (S), Q1.2 (S), Q1.3 (S), U4.1 (VI); also elsewhere on the board
GND: C10.2, C11.2, C12.2, C13.2, C14.2, D2.1 (K), J8.1, Q1.4 (G), U4.2 (GND), U5.3 (GND); also elsewhere on the board
unnamed: D2.2 (A), R6.2
unnamed: J8.2, Q1.5 (D), Q1.6 (D), Q1.7 (D), Q1.8 (D)
unnamed: R27.2, U5.2 (OUT)
VDDA: C14.1, R27.1; also elsewhere on the board

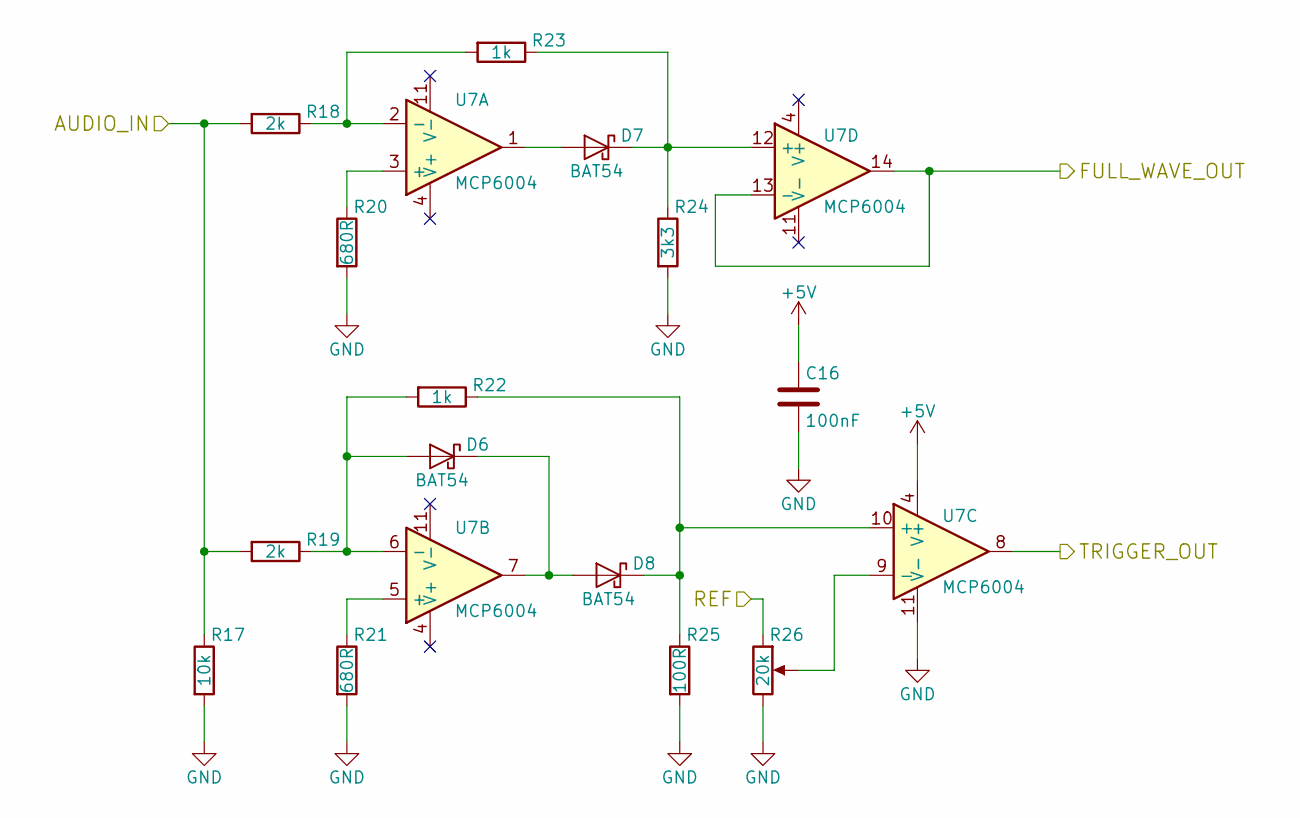
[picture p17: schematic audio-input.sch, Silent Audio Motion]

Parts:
C15: 100nF; C_0805; Manufacturer Part Number C0805C104J5RACTU
D3, D4, D5: BAT54; D_SOD-123; Manufacturer Part Number BAT54GWJ
R7: 10k; R_0805_HandSoldering; Manufacturer Part Number CR0805-JW-103ELF
R8, R9: 2k; R_0805_HandSoldering; Manufacturer Part Number CR0805-FX-2001ELF
R10, R11: 680R; R_0805_HandSoldering; Manufacturer Part Number CR0805-FX-6800ELF
R12, R13: 1k; R_0805_HandSoldering; Manufacturer Part Number CR0805-FX-1001ELF
R14: 3k3; R_0805_HandSoldering; Manufacturer Part Number CR0805-FX-3301ELF
R15: 100R; R_0805_HandSoldering; Manufacturer Part Number CR0805-FX-1000ELF
R16: 20k; Potentiometer_Trimmer_Bourns_3299P; Manufacturer Part Number 36KR20KLF
U6: MCP6004; TSSOP-14_4.4x5mm_Pitch0.65mm; Manufacturer Part Number MCP6004-I/ST

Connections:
+5V: C15.1, U6.4 (V+); also elsewhere on the board
/Audio input L/AUDIO_IN: R7.1, R8.2, R9.2; also elsewhere on the board
/FW_L: U6.13 (-), U6.14; also elsewhere on the board
/REF_L: R16.1; also elsewhere on the board
/TRG_L: U6.8; also elsewhere on the board
GND: C15.2, R7.2, R10.2, R11.2, R14.2, R15.2, R16.3, U6.11 (V-); also elsewhere on the board
unnamed: D3.1 (K), D5.2 (A), U6.7
unnamed: D3.2 (A), R9.1, R12.2, U6.6 (-)
unnamed: D4.1 (K), R13.1, R14.1, U6.12 (+)
unnamed: D4.2 (A), U6.1
unnamed: D5.1 (K), R12.1, R15.1, U6.10 (+)
unnamed: R10.1, U6.3 (+)
unnamed: R11.1, U6.5 (+)
unnamed: R8.1, R13.2, U6.2 (-)
unnamed: R16.2, U6.9 (-)

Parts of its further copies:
C16: 100nF; C_0805; Manufacturer Part Number C0805C104J5RACTU
D6, D7, D8: BAT54; D_SOD-123; Manufacturer Part Number BAT54GWJ
R17: 10k; R_0805_HandSoldering; Manufacturer Part Number CR0805-JW-103ELF
R18, R19: 2k; R_0805_HandSoldering; Manufacturer Part Number CR0805-FX-2001ELF
R20, R21: 680R; R_0805_HandSoldering; Manufacturer Part Number CR0805-FX-6800ELF
R22, R23: 1k; R_0805_HandSoldering; Manufacturer Part Number CR0805-FX-1001ELF
R24: 3k3; R_0805_HandSoldering; Manufacturer Part Number CR0805-FX-3301ELF
R25: 100R; R_0805_HandSoldering; Manufacturer Part Number CR0805-FX-1000ELF
R26: 20k; Potentiometer_Trimmer_Bourns_3299P; Manufacturer Part Number 36KR20KLF
U7: MCP6004; TSSOP-14_4.4x5mm_Pitch0.65mm; Manufacturer Part Number MCP6004-I/ST

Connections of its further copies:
+5V: C16.1, U7.4 (V+); also elsewhere on the board
/Audio input R/AUDIO_IN: R17.1, R18.2, R19.2; also elsewhere on the board
/FW_R: U7.13 (-), U7.14; also elsewhere on the board
/REF_R: R26.1; also elsewhere on the board
/TRG_R: U7.8; also elsewhere on the board
GND: C16.2, R17.2, R20.2, R21.2, R24.2, R25.2, R26.3, U7.11 (V-); also elsewhere on the board
unnamed: D6.1 (K), D8.2 (A), U7.7
unnamed: D6.2 (A), R19.1, R22.2, U7.6 (-)
unnamed: D7.1 (K), R23.1, R24.1, U7.12 (+)
unnamed: D7.2 (A), U7.1
unnamed: D8.1 (K), R22.1, R25.1, U7.10 (+)
unnamed: R18.1, R23.2, U7.2 (-)
unnamed: R20.1, U7.3 (+)
unnamed: R21.1, U7.5 (+)
unnamed: R26.2, U7.9 (-)

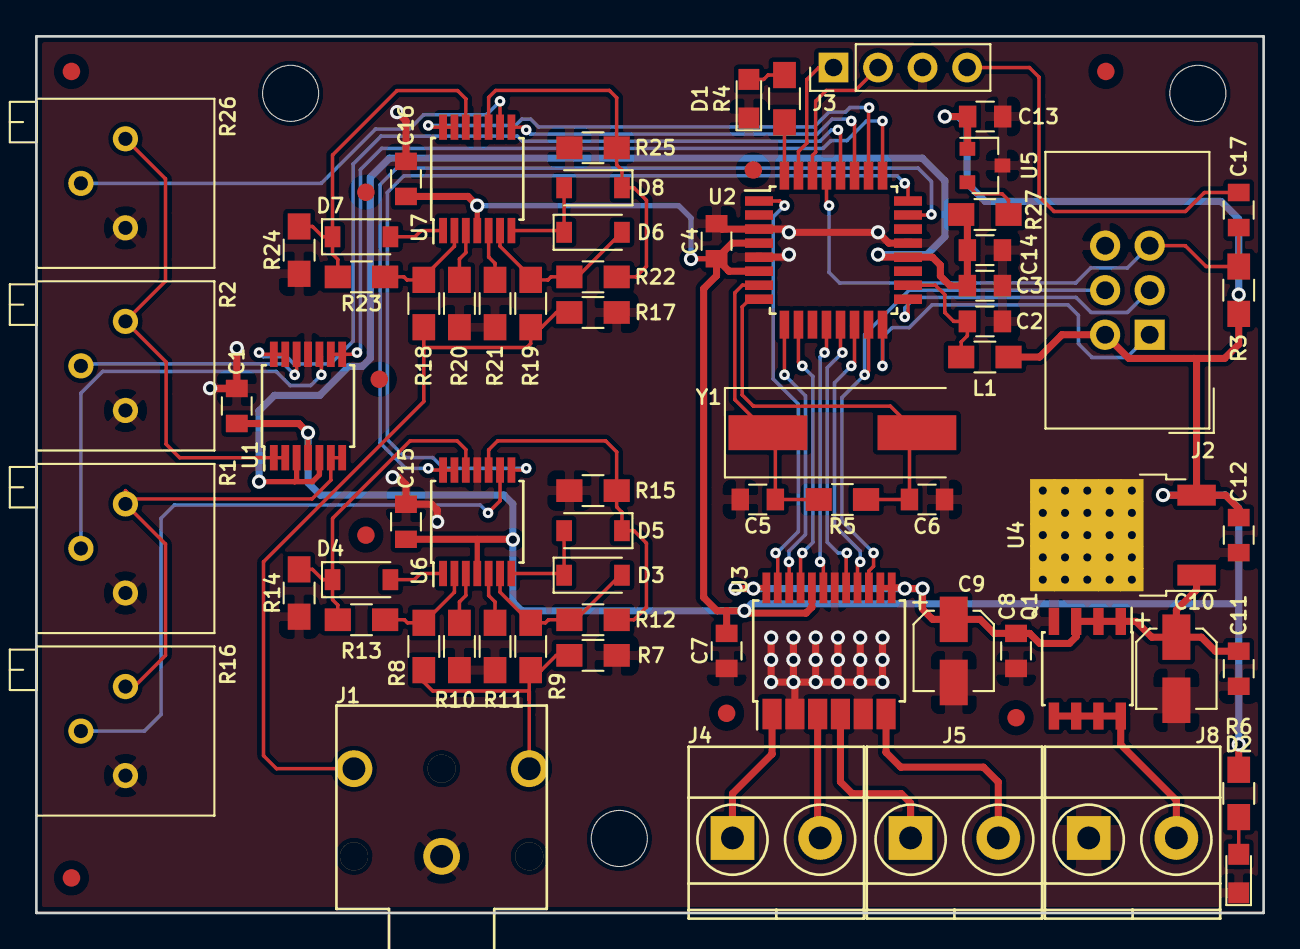
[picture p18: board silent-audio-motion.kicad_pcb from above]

Board: 2 copper layers, 70.0 x 50.0 mm, 68 parts (0 on the bottom side), 59 nets.

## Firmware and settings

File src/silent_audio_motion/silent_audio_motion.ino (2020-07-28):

#define STBY                    8
#define APWM                    3
#define AIN1                    6
#define AIN2                    5
#define BPWM                    11
#define BIN1                    9
#define BIN2                    10
#define FW_L                    A0
#define TRG_L                   A1
#define ADJ_L                   A2
#define FW_R                    A3
#define TRG_R                   A4
#define ADJ_R                   A5
#define DEBUG                   2

#define BUFFER_SIZE             32  // Tamaño de buffer de datos del flujo analógico de entrada
#define STANDBY_THRESHOLD       10  // Por debajo de este nivel permanece apagado, muestra nivel de entrada bajo
#define SATURATION_THRESHOLD    900 // Por encima de este nivel muestra saturación de entrada

void setup() {
    analogReference(EXTERNAL);
    pinMode(STBY, OUTPUT);
    pinMode(APWM, OUTPUT);
    pinMode(AIN1, OUTPUT);
    pinMode(AIN2, OUTPUT);
    pinMode(BPWM, OUTPUT);
    pinMode(BIN1, OUTPUT);
    pinMode(BIN2, OUTPUT);
    pinMode(DEBUG, OUTPUT);
    pinMode(TRG_L, INPUT);
    pinMode(TRG_R, INPUT);
    TCCR2B = TCCR2B & B11111000 | B00000001;    // set timer 2 divisor to 1 for PWM frequency of 31372.55 Hz
    ADCSRA = ADCSRA & B11111000 | B00000100;    // set ADC capture time divider to 16, 20µs for each capture
    Serial.begin(115200);
}

void loop() {
    static boolean input_standby_l = false;
    static boolean input_standby_r = false;
    static boolean input_saturation_l = false;
    static boolean input_saturation_r = false;
    static boolean output_clipping_l = false;
    static boolean output_clipping_r = false;
    static unsigned int channel_buffer_l[BUFFER_SIZE];
    static unsigned int channel_buffer_r[BUFFER_SIZE];
    static unsigned int peak_value_l = 0;
    static unsigned int peak_value_r = 0;
    static unsigned int adjust_l = 0;
    static unsigned int adjust_r = 0;

    read_channel(channel_buffer_l, channel_buffer_r);
    read_adjust(&adjust_l, &adjust_r); //each 250ms
    search_peak_value(&peak_value_l, channel_buffer_l, &peak_value_r, channel_buffer_r);
    process_channel(input_standby_l && input_standby_r, channel_buffer_l, adjust_l, channel_buffer_r, adjust_r);
    set_status(&input_standby_l, &input_saturation_l, &output_clipping_l, peak_value_l, adjust_l, &input_standby_r, &input_saturation_r, &output_clipping_r, peak_value_r, adjust_r); //each 500ms
    display_status(input_standby_l && input_standby_r, input_saturation_l || input_saturation_r, output_clipping_l || output_clipping_r);
}

// Lee las entradas analógicas de ambos canales y los almacena en la primera posición de un array
// Requiere:
//  value_l: array para el canal L, de tamaño BUFFER_SIZE
//  value_r: array para el canal R, de tamaño BUFFER_SIZE
void read_channel(unsigned int *value_l, unsigned int *value_r) {
    for (int i = BUFFER_SIZE - 2; i >= 0; i--) {
        value_l[i + 1] = value_l[i];
        value_r[i + 1] = value_r[i];
    }
    value_l[0] = analogRead(FW_L);
    value_r[0] = analogRead(FW_R);
}

// Lee las entradas del trimmer ADJ de ambos canales y las almacena en variables. Realiza una lectura cada 250ms
// Requiere:
//  adjust_l: puntero de la variable para guardar el valor del canal L
//  adjust_r: puntero de la variable para guardar el valor del canal R
void read_adjust(unsigned int *adjust_l, unsigned int *adjust_r) {
    static unsigned long t = 0;

    if (millis() - t >= 250) {
        t = millis();
        *adjust_l = analogRead(ADJ_L);
        *adjust_r = analogRead(ADJ_R);
    }
}

// Busca el valor de pico de las últimas lecturas de los canales analógicos de entrada. Tamaño del buffer de búsqueda BUFFER_SIZE² samples
// Requiere:
//  peak_l: puntero de la variable para guardar el valor de pico del canal L
//  value_l: array de muestras de entrada del canal L
//  peak_r: puntero de la variable para guardar el valor de pico del canal R
//  value_r: array de muestras de entrada del canal R
void search_peak_value(unsigned int *peak_l, unsigned int *value_l, unsigned int *peak_r, unsigned int *value_r) {
    unsigned int max_l = 0;
    unsigned int max_r = 0;
    static unsigned int counter = 0;
    static unsigned int max_value_l[BUFFER_SIZE];
    static unsigned int max_value_r[BUFFER_SIZE];

    counter++;
    if (counter == BUFFER_SIZE) {
        counter = 0;
        for (int i = 0; i < BUFFER_SIZE; i++) {
            if (value_l[i] > max_l) max_l = value_l[i];
            if (value_r[i] > max_r) max_r = value_r[i];
        }
        for (int i = BUFFER_SIZE - 2; i >= 0; i--) {
            max_value_l[i + 1] = max_value_l[i];
            max_value_r[i + 1] = max_value_r[i];
        }
        max_value_l[0] = max_l;
        max_value_r[0] = max_r;
    }
    *peak_l = 0;
    *peak_r = 0;
    for (int i = 0; i < BUFFER_SIZE; i++) {
        if (max_value_l[i] > *peak_l) *peak_l = max_value_l[i];
        if (max_value_r[i] > *peak_r) *peak_r = max_value_r[i];
    }
}

// Genera la señal de salida en función de los valores de entrada
// Requiere:
//  input_min: indicador de si ambas entradas están en reposo
//  value_l: array de muestras de entrada del canal L
//  adjust_l: valor del trimmer ADJ del canal L
//  value_r: array de muestras de entrada del canal R
//  adjust_r: valor del trimmer ADJ del canal R
void process_channel(boolean input_min, unsigned int *value_l , unsigned int adjust_l, unsigned int *value_r , unsigned int adjust_r) {
    boolean polarity_l = false;
    boolean polarity_r = false;
    unsigned char sample_l = 0;
    unsigned char sample_r = 0;

    if (!input_min) {
        digitalWrite(STBY, HIGH);
        polarity_l = digitalRead(TRG_L);
        digitalWrite(AIN1, !polarity_l);
        digitalWrite(AIN2, polarity_l);
        sample_l = constrain(map(value_l[0], 0, adjust_l, 0, 255), 0, 255);
        analogWrite(APWM, sample_l);
        polarity_r = digitalRead(TRG_R);
        digitalWrite(BIN1, !polarity_r);
        digitalWrite(BIN2, polarity_r);
        sample_r = constrain(map(value_r[0], 0, adjust_r, 0, 255), 0, 255);
        analogWrite(BPWM, sample_r);
    }
    else digitalWrite(STBY, LOW);
}

// Establece los indicadores de estado. Se actualiza cada 500ms
// Requiere:
//  input_min_l: puntero donde se guarda el estado de entrada en reposo para el canal L
//  input_max_l: puntero donde se guarda el estado de entrada saturada para el canal L
//  output_l: puntero donde se guarda el estado de clipping en salida para el canal L
//  peak_l: valor de pico de las muestras de entrada del canal L
//  adjust_l: valor del trimmer ADJ del canal L
//  input_min_r: puntero donde se guarda el estado de entrada en reposo para el canal R
//  input_max_r: puntero donde se guarda el estado de entrada saturada para el canal R
//  output_r: puntero donde se guarda el estado de clipping en salida para el canal R
//  peak_r: valor de pico de las muestras de entrada del canal R
//  adjust_r: valor del trimmer ADJ del canal R
void set_status(boolean *input_min_l, boolean *input_max_l, boolean *output_l, unsigned int peak_l, unsigned int adjust_l, boolean *input_min_r, boolean *input_max_r, boolean *output_r, unsigned int peak_r, unsigned int adjust_r) {
    static unsigned long t = 0;

    if (millis() - t >= 500) {
        t = millis();
        if (peak_l < STANDBY_THRESHOLD) *input_min_l = true;
        else *input_min_l = false;
        if (peak_r < STANDBY_THRESHOLD) *input_min_r = true;
        else *input_min_r = false;
        if (peak_l > SATURATION_THRESHOLD) *input_max_l = true;
        else *input_max_l = false;
        if (peak_r > SATURATION_THRESHOLD) *input_max_r = true;
        else *input_max_r = false;
        if (peak_l > adjust_l) *output_l = true;
        else *output_l = false;
        if (peak_r > adjust_r) *output_r = true;
        else *output_r = false;
    }
}

// Muestra el estado actual usando un LED
// Requiere:
//  input_min: indicador de si ambas entradas están en reposo
//  input_max: indicador de si alguna de las entradas está saturada
//  output: indicador de si alguna de las salidas hace clipping
void display_status(boolean input_min, boolean input_max, boolean output) {
    if (input_min) digitalWrite(DEBUG, HIGH);
    else if (input_max) digitalWrite(DEBUG, millis() & 0x20);
    else if (output) digitalWrite(DEBUG, millis() & 0x80);
    else digitalWrite(DEBUG, LOW);
}

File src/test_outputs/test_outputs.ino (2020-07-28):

/*
 * TIPOS DE FORMA DE ONDA, NO TOCAR
 */
#define SIN         1       // SENOIDAL
#define SAW         2       // DIENTE DE SIERRA
#define TRI         3       // TRIANGULAR
#define SQR         4       // CUADRADA

/*
 * DEFINICION DE LA ONDA, TOCAR AQUI
 */
#define HZ          2.00    // NECESARIO ESTABLECER CON DOS DECIMALES
#define VOL         1.00    // VALOR ENTRE 0.00 y 1.00, ESTABLECER CON DOS DECIMALES
#define WAVEFORM    SIN     // ELEGIR: SIN, SAW, TRI, SQR
//#define OSCOPE              // PERMITE VER LA ONDA DE SALIDA USANDO EL SERIAL_PLOTTER
                            //   PUEDE AFECTAR A LA FRECUENCIA, DESCOMENTAR PARA USAR

/*
 * DEFINES GENERALES, NO TOCAR
 */
#define STBY        8
#define APWM        3
#define AIN1        6
#define AIN2        5
#define BPWM        11
#define BIN1        9
#define BIN2        10
#define FW_L        A0
#define TRG_L       A1
#define ADJ_L       A2
#define FW_R        A3
#define TRG_R       A4
#define ADJ_R       A5
#define DEBUG       2
#define DELAY       (1000000/(512*HZ))

//https://www.daycounter.com/Calculators/Sine-Generator-Calculator2.phtml
const unsigned char sinPWM[]={0,0,0,1,1,1,2,2,3,4,4,5,6,7,8,9,
11,12,13,15,16,18,20,21,23,25,27,29,31,33,35,37,
39,42,44,46,49,51,54,56,59,62,64,67,70,73,76,79,
81,84,87,90,93,96,99,103,106,109,112,115,118,121,124,128,
128,131,134,137,140,143,146,149,152,156,159,162,165,168,171,174,
176,179,182,185,188,191,193,196,199,201,204,206,209,211,213,216,
218,220,222,224,226,228,230,232,234,235,237,239,240,242,243,244,
246,247,248,249,250,251,251,252,253,253,254,254,254,255,255,255,
255,255,255,255,254,254,253,253,252,252,251,250,249,248,247,246,
245,244,242,241,239,238,236,235,233,231,229,227,225,223,221,219,
217,215,212,210,207,205,202,200,197,195,192,189,186,184,181,178,
175,172,169,166,163,160,157,154,151,148,145,142,138,135,132,129,
126,123,120,117,113,110,107,104,101,98,95,92,89,86,83,80,
77,74,71,69,66,63,60,58,55,53,50,48,45,43,40,38,
36,34,32,30,28,26,24,22,20,19,17,16,14,13,11,10,
9,8,7,6,5,4,3,3,2,2,1,1,0,0,0,0};

const unsigned char sawPWM[]={0,1,2,3,4,5,6,7,8,9,10,11,12,13,14,15,
16,17,18,19,20,21,22,23,24,25,26,27,28,29,30,31,
32,33,34,35,36,37,38,39,40,41,42,43,44,45,46,47,
48,49,50,51,52,53,54,55,56,57,58,59,60,61,62,63,
64,65,66,67,68,69,70,71,72,73,74,75,76,77,78,79,
80,81,82,83,84,85,86,87,88,89,90,91,92,93,94,95,
96,97,98,99,100,101,102,103,104,105,106,107,108,109,110,111,
112,113,114,115,116,117,118,119,120,121,122,123,124,125,126,127,
128,129,130,131,132,133,134,135,136,137,138,139,140,141,142,143,
144,145,146,147,148,149,150,151,152,153,154,155,156,157,158,159,
160,161,162,163,164,165,166,167,168,169,170,171,172,173,174,175,
176,177,178,179,180,181,182,183,184,185,186,187,188,189,190,191,
192,193,194,195,196,197,198,199,200,201,202,203,204,205,206,207,
208,209,210,211,212,213,214,215,216,217,218,219,220,221,222,223,
224,225,226,227,228,229,230,231,232,233,234,235,236,237,238,239,
240,241,242,243,244,245,246,247,248,249,250,251,252,253,254,255};

const unsigned char triPWM[]={0,2,4,6,8,10,12,14,16,18,20,22,24,26,28,30,
32,34,36,38,40,42,44,46,48,50,52,54,56,58,60,62,
64,66,68,70,72,74,76,78,80,82,84,86,88,90,92,94,
96,98,100,102,104,106,108,110,112,114,116,118,120,122,124,126,
128,130,132,134,136,138,140,142,144,146,148,150,152,154,156,158,
160,162,164,166,168,170,172,174,176,178,180,182,184,186,188,190,
192,194,196,198,200,202,204,206,208,210,212,214,216,218,220,222,
224,226,228,230,232,234,236,238,240,242,244,246,248,250,252,254,
254,252,250,248,246,244,242,240,238,236,234,232,230,228,226,224,
222,220,218,216,214,212,210,208,206,204,202,200,198,196,194,192,
190,188,186,184,182,180,178,176,174,172,170,168,166,164,162,160,
158,156,154,152,150,148,146,144,142,140,138,136,134,132,130,128,
126,124,122,120,118,116,114,112,110,108,106,104,102,100,98,96,
94,92,90,88,86,84,82,80,78,76,74,72,70,68,66,64,
62,60,58,56,54,52,50,48,46,44,42,40,38,36,34,32,
30,28,26,24,22,20,18,16,14,12,10,8,6,4,4,0};

const unsigned char sqrPWM[]={0,127,255,255,255,255,255,255,255,255,255,255,255,255,255,255,
255,255,255,255,255,255,255,255,255,255,255,255,255,255,255,255,
255,255,255,255,255,255,255,255,255,255,255,255,255,255,255,255,
255,255,255,255,255,255,255,255,255,255,255,255,255,255,255,255,
255,255,255,255,255,255,255,255,255,255,255,255,255,255,255,255,
255,255,255,255,255,255,255,255,255,255,255,255,255,255,255,255,
255,255,255,255,255,255,255,255,255,255,255,255,255,255,255,255,
255,255,255,255,255,255,255,255,255,255,255,255,255,255,255,255,
255,255,255,255,255,255,255,255,255,255,255,255,255,255,255,255,
255,255,255,255,255,255,255,255,255,255,255,255,255,255,255,255,
255,255,255,255,255,255,255,255,255,255,255,255,255,255,255,255,
255,255,255,255,255,255,255,255,255,255,255,255,255,255,255,255,
255,255,255,255,255,255,255,255,255,255,255,255,255,255,255,255,
255,255,255,255,255,255,255,255,255,255,255,255,255,255,255,255,
255,255,255,255,255,255,255,255,255,255,255,255,255,255,255,255,
255,255,255,255,255,255,255,255,255,255,255,255,255,255,127,0};

void setup() {
    analogReference(EXTERNAL);
    pinMode(STBY, OUTPUT);
    pinMode(APWM, OUTPUT);
    pinMode(AIN1, OUTPUT);
    pinMode(AIN2, OUTPUT);
    pinMode(BPWM, OUTPUT);
    pinMode(BIN1, OUTPUT);
    pinMode(BIN2, OUTPUT);
    pinMode(DEBUG, OUTPUT);
    pinMode(TRG_L, INPUT);
    pinMode(TRG_R, INPUT);
    TCCR2B = TCCR2B & B11111000 | B00000001;    // set timer 2 divisor to 1 for PWM frequency of 31372.55 Hz
#ifdef OSCOPE
    Serial.begin(115200);
#endif
}

void loop() {
    static boolean polarity = false;
    unsigned char sample = 0;

    digitalWrite(DEBUG, polarity);
    digitalWrite(STBY, HIGH);
    digitalWrite(AIN1, !polarity);
    digitalWrite(AIN2, polarity);
    digitalWrite(BIN1, !polarity);
    digitalWrite(BIN2, polarity);
    for (unsigned char i = 0; i < 255; i++) {
#if WAVEFORM == SIN
        sample = sinPWM[i] * VOL;
#elif WAVEFORM == SAW
        sample = sawPWM[i] * VOL;
#elif WAVEFORM == TRI
        sample = triPWM[i] * VOL;
#elif WAVEFORM == SQR
        sample = sqrPWM[i] * VOL;
#endif
#ifdef OSCOPE
        if (polarity) Serial.println(sample);
        else Serial.println(-sample);
#endif
        analogWrite(APWM, sample);
        analogWrite(BPWM, sample);
        delayMicroseconds(DELAY);
    }
    polarity = !polarity;
}

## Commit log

2019-11-03 añadido application note de rectificadores
2019-11-03 añadido diseño de pcb
    [audio-input.sch, power-supply.sch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]
2020-02-25 subido diseño 3d
    [base.stl, bridge.stl, silent-audio-motion.scad]
2020-07-28 actualizado diseño 3d
    [bridge.stl, silent-audio-motion.scad]
2020-07-28 añadidos codigos de prueba y calibracion
2020-07-28 corregido problema con referencia analogica
    [audio-input.sch, power-supply.sch, silent-audio-motion.kicad_pcb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]
2020-07-28 añadido pin DTR para reset en cabecera UART
    [audio-input.sch, power-supply.sch, silent-audio-motion.kicad_pcb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]
2020-07-28 subido nuevo firmware de control
2020-07-28 actualizado cajetin de datos
    [audio-input.sch, power-supply.sch, silent-audio-motion.sch]
2020-07-28 generado PDF de PCB
2020-07-28 regenerados gerbers
    [silent-audio-motion-back.gbl, silent-audio-motion-front.gtl, silent-audio-motion-mask-back.gbs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]
2020-08-19 añadido datasheet de potenciometro pv36
    [audio-input.sch, silent-audio-motion.sch]
2020-08-19 actualizado 3d con componentes de la pcb
    [silent-audio-motion.scad]

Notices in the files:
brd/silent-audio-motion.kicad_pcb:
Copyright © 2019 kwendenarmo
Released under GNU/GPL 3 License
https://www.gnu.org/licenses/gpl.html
